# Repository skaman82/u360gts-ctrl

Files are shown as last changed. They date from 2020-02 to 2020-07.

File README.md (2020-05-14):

# u360gts-ctrl
u360gts Extension for the Mini-Case

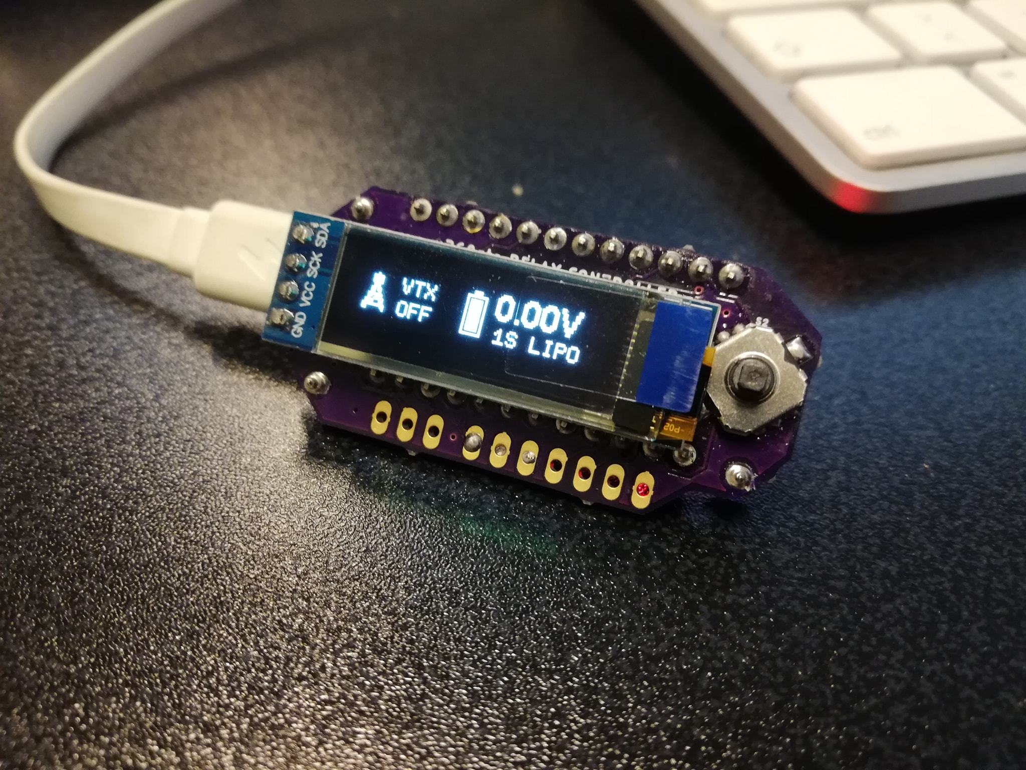
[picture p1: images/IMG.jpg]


This has the following functions:

• Turn ON/OFF the VTX</br>
• SmartAudio channel control (SA 2+ Version not supported, for unify nano you will need a 10k pull-down resistor on SA)</br>
• Battery monitoring</br>
• Controlls pan servo manually to allow to get to the screws of the case</br>
• Automatic parking mode to align the tracker again</br>

# PARTS
• Provided PCB

• Arduino Pro Micro (Leonardo) 3.3V
https://de.aliexpress.com/item/32992577032.html
If you have a 5V version, just replace the VREG on the board with this one: MIC5205-3.3YM5-TR

• 1206 4.7k resistor (R3)</br>
• 1206 27k resistor (R1)</br>
• 1206 100nf capacitor (C3)</br>
• 4x 0603 10k resistor (R2, R4, R5, R6)</br>
• 0603 1k resistor (R7)</br>
• IRLML6402 Mosfet (SOT23-3)</br>
• 2x BC848B Transistor (SOT23-3) (Q1, Q2)</br>

• 5-way tact switch
https://de.aliexpress.com/item/32860774374.html

• 128x32 I2C OLED Display
https://de.aliexpress.com/item/32965469301.html

• CD4066BM switch (SOP14 IC)
https://de.aliexpress.com/item/32461198916.html

• 3mm 940nm IR LEDs (receiver + transmitter) < 
receiver connects to GND and IR+ on the PCB; transmitter connects to 5v (through 100R resistor) and GND in the top box
https://de.aliexpress.com/item/32967272936.html

<strong>UPDATE 11. May 2020</strong><br>
Just spotted a bug on the PCB regarding the IR diode. I just corrected it in the new board file.
If you have the old version of the board, here is a workaround:<br><br>

• Remove R2 (don't throw it away)<br>
• bridge the two pads where R2 was sitting<br>
• solder the R2 to the outer side of the R6<br>
• connect 5V (BZ+) to the outer side of R2<br>
• Connect the IR LED (cathode on IR+, anode on IR-)<br>

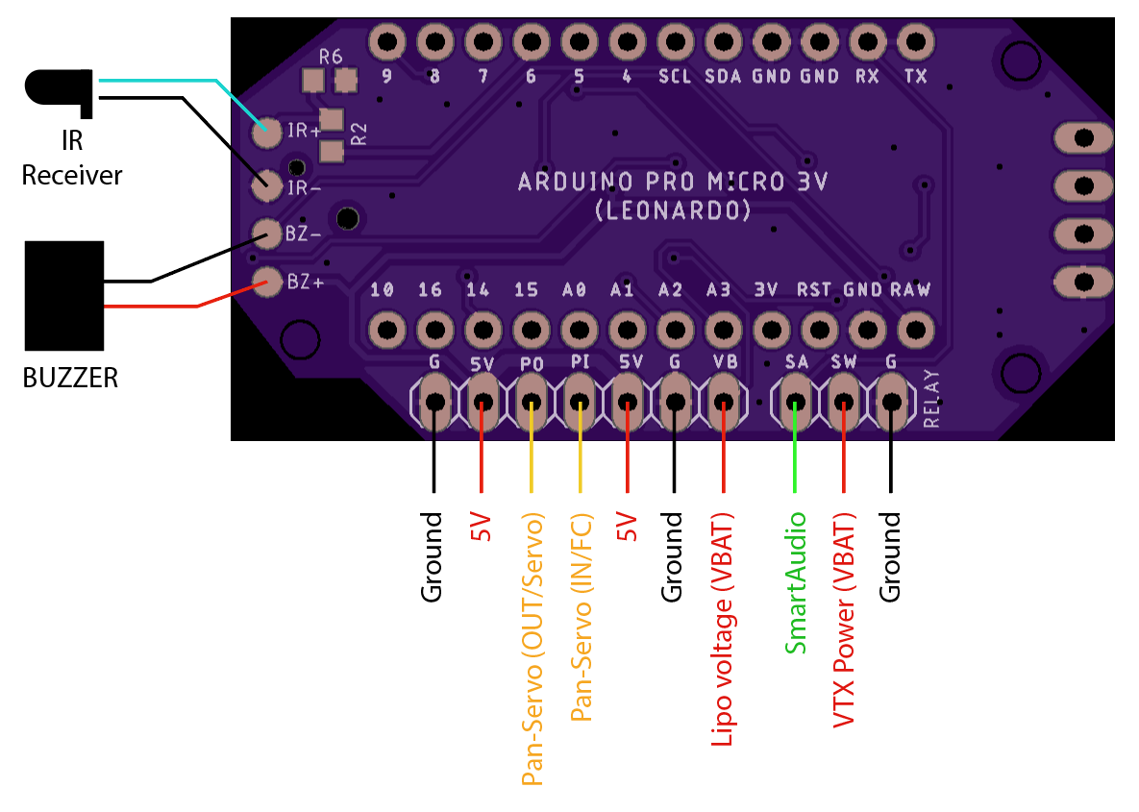
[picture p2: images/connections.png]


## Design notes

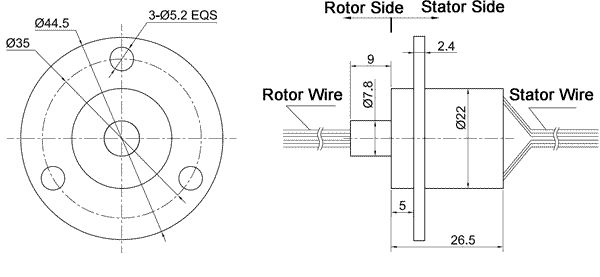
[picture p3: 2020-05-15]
images/slipring_sparkfun_senring.jpg

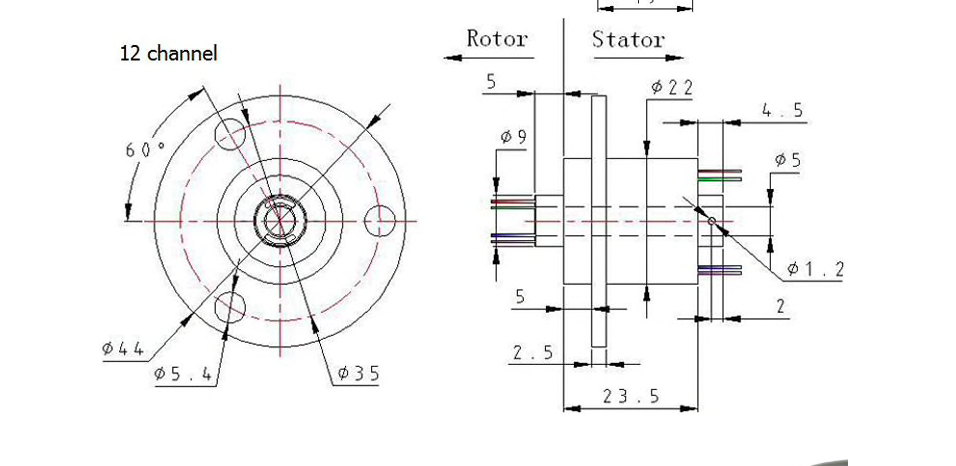
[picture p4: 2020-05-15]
images/slipring_ali.png

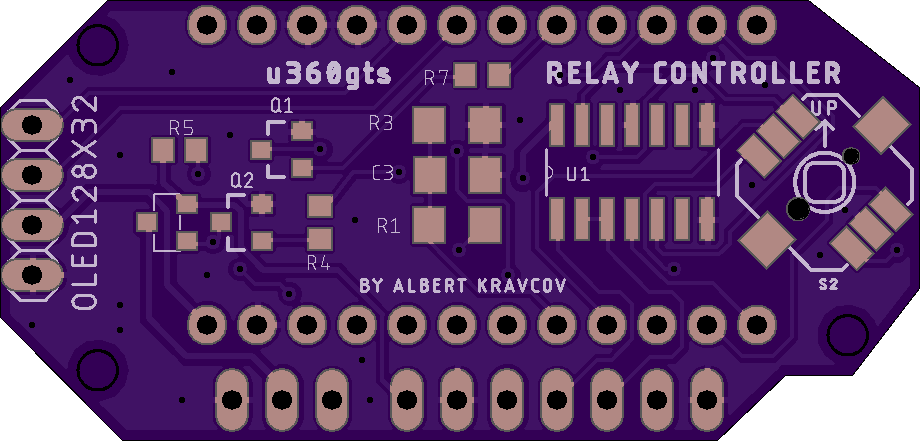
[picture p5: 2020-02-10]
images/Top.png

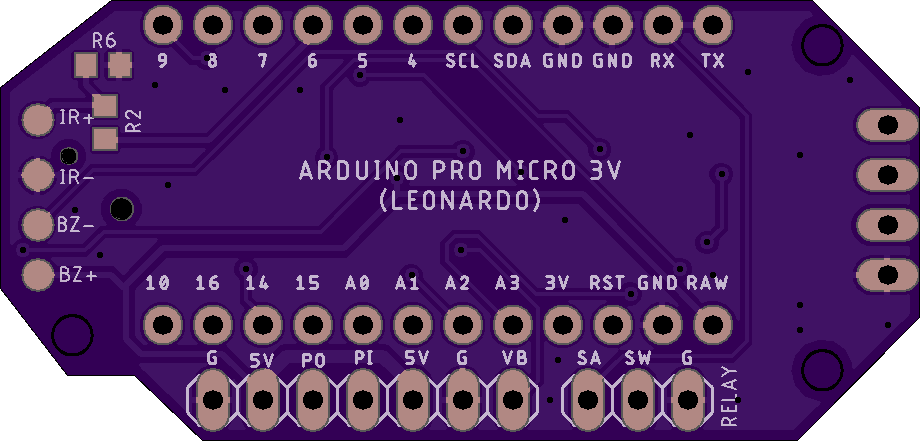
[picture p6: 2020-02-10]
images/Bottom.png

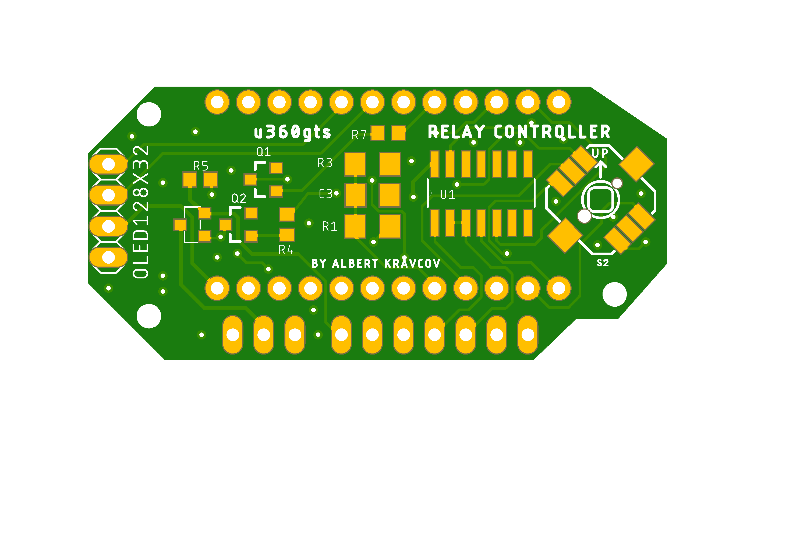
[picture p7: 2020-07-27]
PCB/RelayCTRL_t.png

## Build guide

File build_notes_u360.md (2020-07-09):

# u360gts *(mini build notes)*

### Features

- DIY antenna tracker based on u360gts by Raul Ortega  [https://github.com/raul-ortega/u360gts/](https://github.com/raul-ortega/u360gts/)
- compact design, only 75x75x100cm
- custom PCBs to simplify wiring
- modular tripod mounts
- supports 2-4S, XT60 connector
- 3.5mm analog Video-Out (Fatshark compatible)
- 6-Pin JST-SH breakout port (SW/RX/TX/5V/GND/VIDEO) to support:
  - telemetry relay to GS/tablet
  - connect external VTX
  - OpenLog via softserial
  - Bluetooth Module to configure u360gts
  - ...through 3 configurable pins(SW/RX/TX)
- 6-Pin JST-XH AV IO port (VIDEO/AUD_L/AUD_R/GND/VCC/GND) to connect an external RX-Module (i.e. FR632)
- intergrated Fatshark Module Bay on the head
- Telemetry input via Bluetooth or FSK-Modem, select via switch on head
- advanced controlling through u360gts-ctrl:
 - Turn ON/OFF the VTX
 - SmartAudio channel control
 - Battery monitoring
 - Manually control PAN (to access screws for example)
 - Infrared supported autonomous parking mode to align tracker
 - Bluetooth state-LED visible from outside

##### u360gts-ctrl

- manual PAN control via u360gts-ctl (to access the screws for example)
- Infrared supported Auto-Home position

## General build tips and notes

## u360gts Mini
#### Printing

Print files, PCBs and a complete bill of materials can be found here: https://www.thingiverse.com/thing:4108944

All parts are designed to be printed without supports (only supports touching build plate on some parts).

If your parts suffer from an elephant foot, decrease first layer flow, temperature, horizontal expansion and/or walls. Gear parts might not fit!

#### Assembly PCBs

UPDATE: Do NOT solder the buzzer to the PCB as as it can cause mag interference at this position. Place the buzzer somwhere at the bottom and wire it to the pads.

Isolate the back of the 128x64 display and remove the plastics on the pin headers for correct fit.

add a little button to the boot pins of the FC & thank me later
	
#### Assembly body

Prefit IR diode to the hole in the body-lid (used to reach home parking position) and if needed open hole with a drill. Same in the IR-LED in the bottom of the head.

Bottom left nut holder might needs a trim to ensure clearance to the 9pin header of the power PCB.

Place nuts early and fix with some glue.

The gears should not sit on each other and tilt the head to the side if correctly assembled.

#### Assembly head

Two versions of the slipring are currently supported. 23mm (AliExpress) and 26mm long (Sparkfun ROB-13065). Choose your "Bearing\_upper\_insert" STL accordingly.

Cut down the two little spars on the tilt servo so it seats flush on the wall

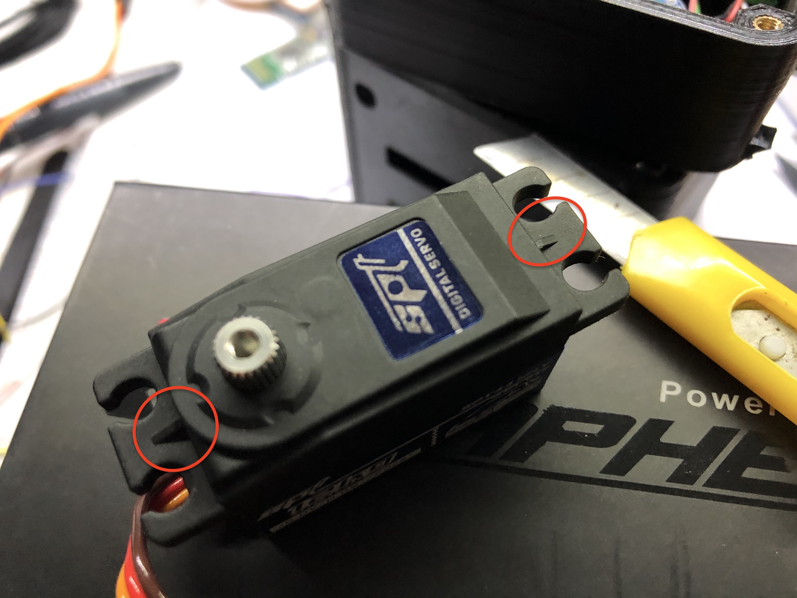
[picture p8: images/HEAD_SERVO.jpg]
Servo spars


Solder the IO board to the slipring from "behind" for easier cable routing

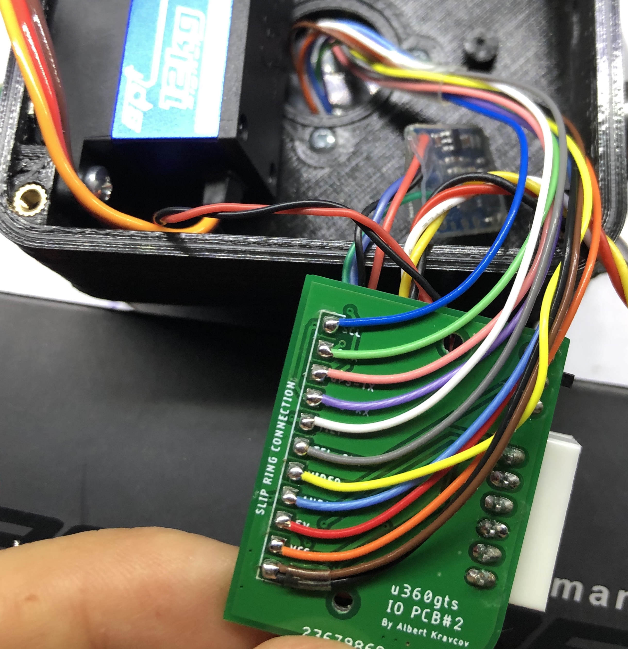
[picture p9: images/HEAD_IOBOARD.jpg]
IO board


Make sure all components (BT Module, RX Board etc.) are well isolated on the back to not create a short when closing the lid

Before mounting the servo-disc and the tracker arm, ensure the tilt servo is at 0° deg. If you dont own a servotester, connect to the GUI and move the servo using the slider. 

Once the arm is mounted, validate and adjust the tilt endpoints.

Note, the STATE Pin on the RX Board of the lid gets connected to the STATE Pin of your Bluetooth module and will switch on when connected.

#### Wiring

In general, try to route all cables below the FC when possible.

The Buzzer on the OLED board is connected to (+) through OLED-PCB and only needs GND to work. You can use BZ(+) to route 5V to the power PCB and then to power the CTRL board from the pads on top.

BZ(-) on the OLED board can be connected to the FC BZ(-) as well as the CTRL BZ(-) to run by both.

Only 11 pins between the body and the head are needed, use 2 cables for GND through the slipring

For PCBs prior 05/2020 you need to solder the diode in opposite direction (marking should be on the left).
	
Use a second 5V BEC for the PAN servo, as adviced in the partlist and wiring plan. 

RX/TX/SW on the Power PCB are currently not used. You can use those pads to route anything to the 6pin connector on the back (Relay VTX, openLog etc.)

Solder the wires of the OLED PCB to the slipring directing to the top of the PCB in a slight bow.

You can use some hot glue to fix the slipring wires to the pcb as the are fragile and they break easily at the solder joints 

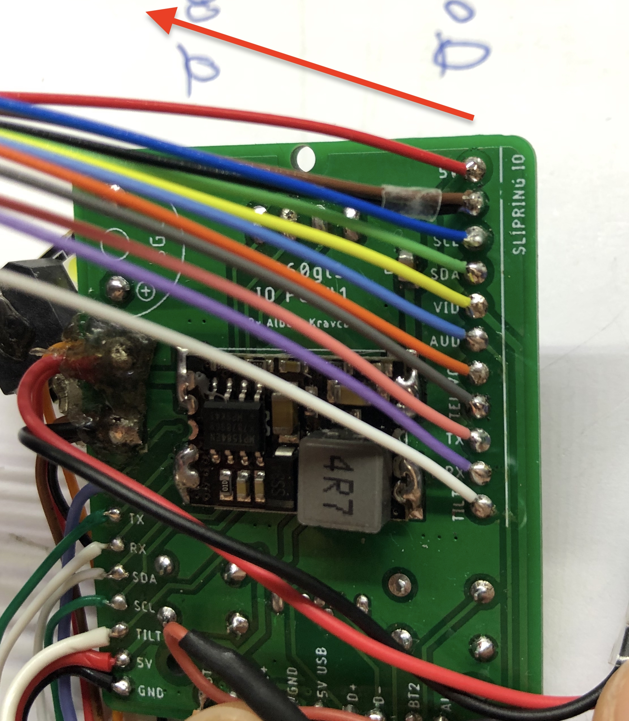
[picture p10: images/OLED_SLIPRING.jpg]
OLED to slipring

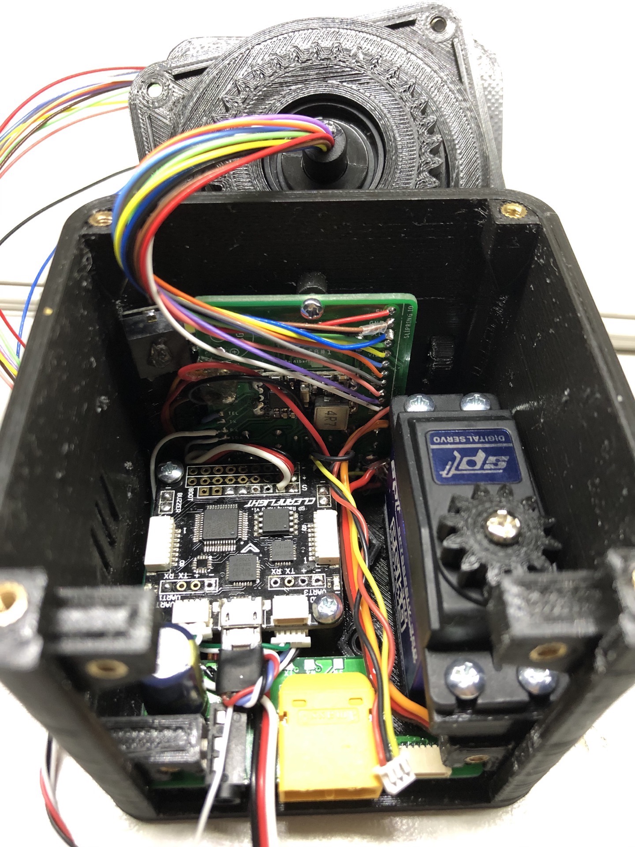
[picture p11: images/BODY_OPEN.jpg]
BODY


#### Wiring schema
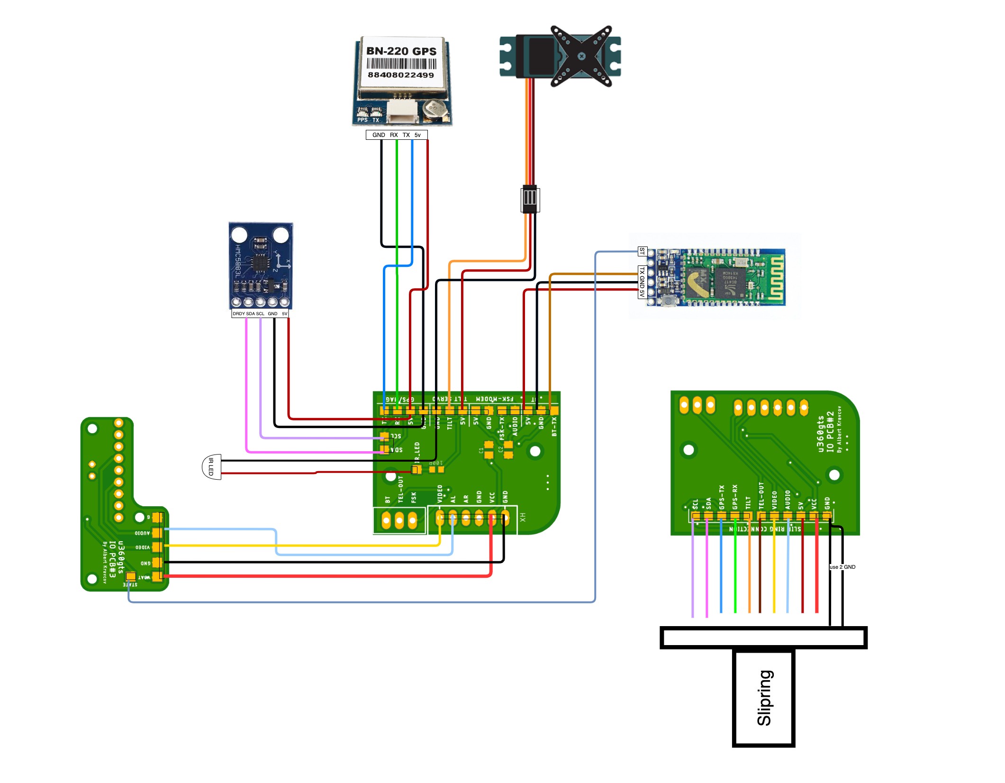
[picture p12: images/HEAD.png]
wiring head

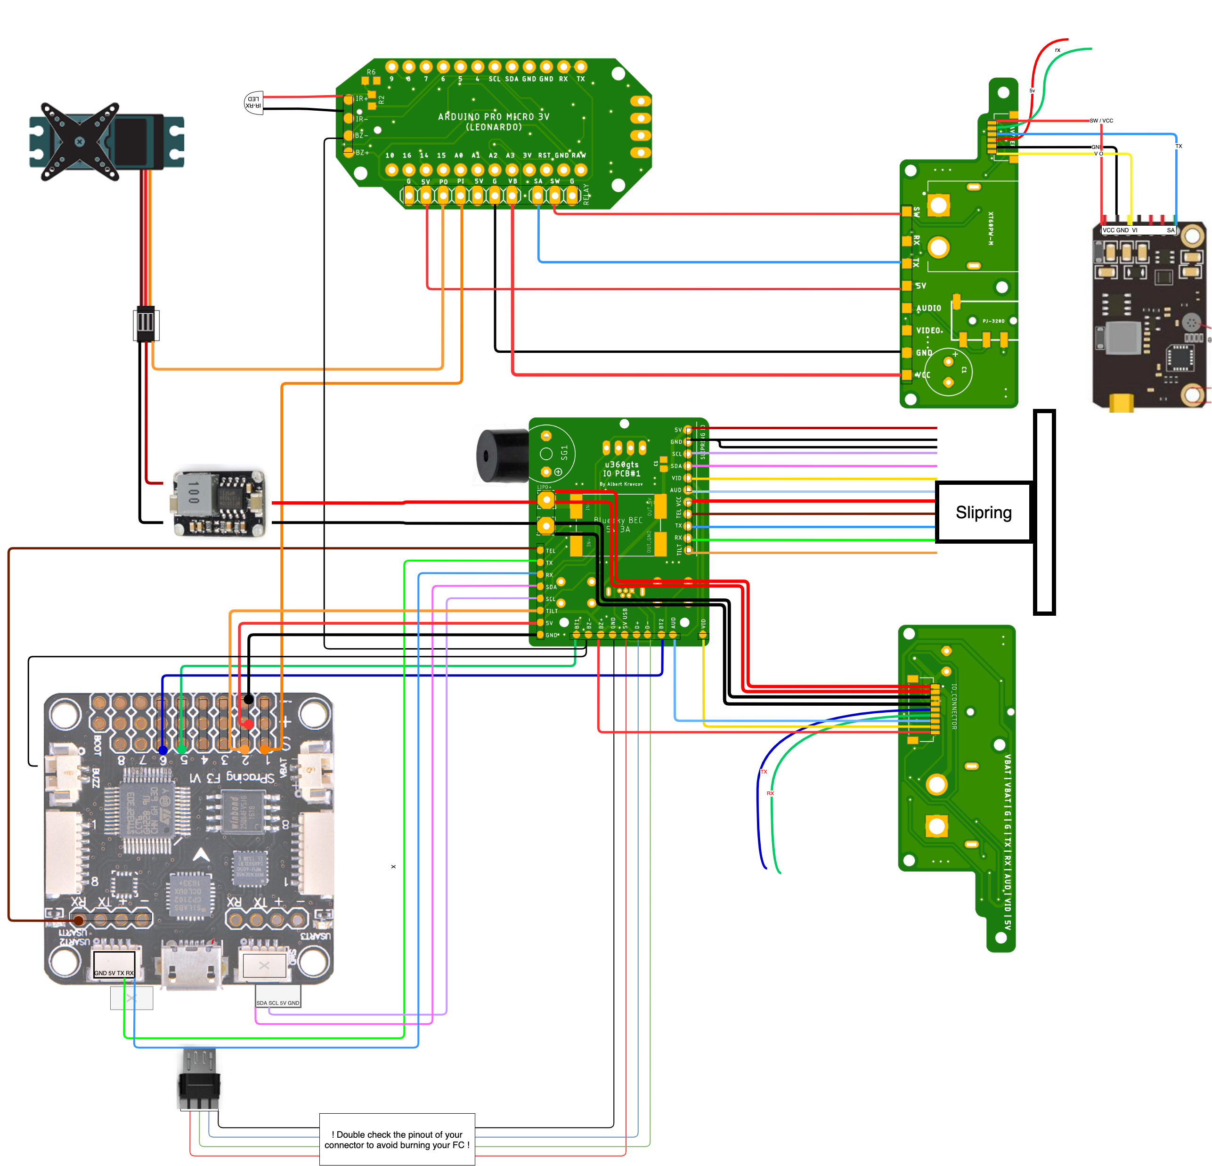
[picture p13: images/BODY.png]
wiring body


## u360gts Controller

#### Hardware

For PCBs prior 05/2020 you need to solder the IR emitter with reverse polarization. The boards also require a little hack to correct a routing mistake:<br>

• Remove R2 (don't throw it away)<br>
• bridge the two pads where R2 was sitting<br>
• solder the R2 to the outer side of the R6<br>
• connect 5V (BZ+) to the outer side of R2<br>
• Connect the IR LED (cathode on IR+, anode on IR-)<br>

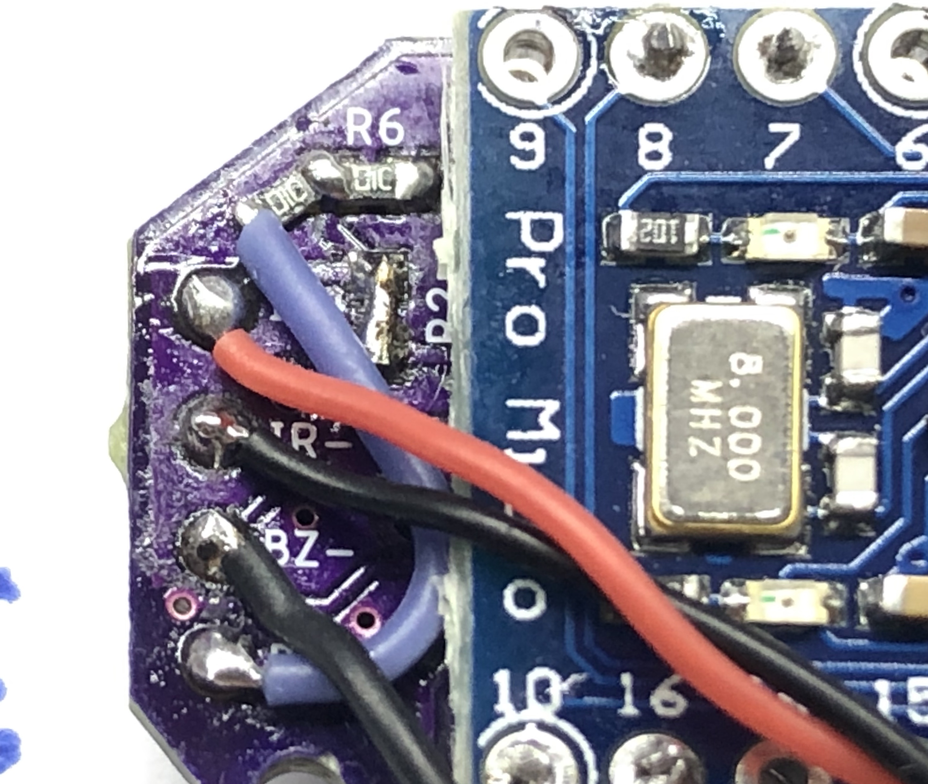
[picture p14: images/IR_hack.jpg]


Use two or three layer of electrical tape between Arduino Pro Micro and the PCB and remove the plastic spacers on the pin headers to ensure clearance to the gear section.

For TBS Unify Pro Nano, which uses SmartAudio Lite, connect a 10K resistor between SA and GND.

The 4066 switch on CTRL PCB with the edge DOWN, when the PCB shows upwards description.

**Important:** The CTRL will provide VCC to the VTX on the SW (switched) pad. Use a mini-BEC if a 5V VTX is planned (i.e. Pololu D24V3F)5 .

Handle the display with exta care. They seem to break easily. Maybe even get spares right away.

#### Software

If your PAN servo does move without command (in manual pan mode, or after the parking is completed), adjust **idle_servo** to match your servo-center-values.

Depending your choice of Arduino you might need to adjust the **voltage_scale**. If default _3.70_ does not match, try _5.56_

If home parking does not work, ensure IR diodes are working (see hardware section) and validate the IR reading in code. 

Enable the following lines in the Relay_CTRL.ino at line 1368-1269:

```
 //    Serial.println(ir_value); 
 //    delay(10); 
```

Then connect via the arduino IDE serial monitor should show the raw IR value like this during the parking process:

```
 522			<--- moving
 522			|
 521			|
 518			|
 452			<--- coming closer
 38				<--- reached ir_stop_value threshold, stops
```

#### Special Arduino Notes

on 3.3V/5V switchable Arduino Pro Micro (16Mhz resonator) use can use the Leonardo target.

on 3.3V fixed Arduinos (8Mhz resonator) follow this guide to enable the Sparkfun Pro Micro 3.3V/8Mhz target:
[https://learn.sparkfun.com/tutorials/pro-micro--fio-v3-hookup-guide/installing-mac--linux](https://github.com/raul-ortega/u360gts/blob/master/wiki/configuration-pan-servo.md)

In case you flashed with the wrong target, and your tty/cu/COM device disappeared, try to force to bootloader by shorting GND+RST twice. Your tty should appear for about 8 seconds to flash the correct hex.
This needs a good timing and might be tricky. 
You might want to extract the avrdude commands after settings the IDE to verbose, then pre-combile the sketch to .hex file and then write the .hex via avrdude manually.
This also works straight directly from Arduino IDE (klick upload, then short reset twice an the micro and it should find a com port and upload the code)

===

## GPS setup

#### Aircraft
Make sure your GPS Module has an update rate at least of 5 Hz

#### Tracker
Configure your Tracker GPS module as described here:
[https://github.com/raul-ortega/u360gts/blob/master/wiki/configuration-gps.md](https://github.com/raul-ortega/u360gts/blob/master/wiki/configuration-gps.md)

If you have a GPS installed and activated, you can set the "Minimun Number of Satellites" (8 is better) in the Configuratior for the home lock. The tracker will automatically determine home position after the set min sat count is reached. The "Continuous Home Update" setting is only usefull if you expecting to move the tracker mid flight.

===

## Telemetry setup

Remark: Telemetry input doesn't work with R9M ACCESS at this time. <br>
In this example I am using Crossfire. CRSF RX connected to an FC UART and serial RX is set to CRSF.
NOTE: CRSF telemetry is transfering a large amount of data. Because of that the BT link might be unstable. 

#### A simple telementy test (CROSSFIRE/X9D/WIRE)
Connect your radio the the flightcontroller via cable.

note: Serial Bridge via Cable through de-inverter ([https://oshpark.com/shared_projects/V3HPfIeN](https://oshpark.com/shared_projects/V3HPfIeN)) needs GND.

```
	Radio		 	 _______________		FC
	GND			|		| 	->	GND
	VCC	->		|  de-inverter	| 	->	n/a
	SIG			|_______________| 	->	RX on FC
```

Set the OpenTX Serial Port to "Telem Mirror" in the Hardware page of your radio settings. Choose CROSSFIRE protocol with baudrate 115200 on the u360gts.

**If "Telem Mirror" is not available, please upgrade your OpenTX later than 2.3x**

Connect a battery on your plane and wait until Sats are found. 

You should receive coordinates of the plane in the tracker now.

===

#### Bluetooth setup

Connect your BT module to an FTDI USB adapter.
Open Arduino serial terminal, make sure you baud 
rate matches the factory settings of the module.
Type AT and you should get an "OK" back if everything is working

The BT module might behave differently based on revision and firmware.

If you are using 2.4 videolink, bluetooth my interfere with your video signal - HC-12 may be a valid alterative as it is working on 433 MHz - it also has a better range (see below) 

##### How to bind a HC-05 FW 3.0 with a HC-05 FW 4.0

Both versions will blink every 2 second if AT mode is active

Get the configuration and address of both modules first.
colon (:) must be entered as comma (,)

###### Master (Radio) FW3.0
	- to enter AT mode no need to push the button, just connect EN and pull high from code
	- PIN needs to be "quoted"
	- request commands like AT+VERSION
	
	AT+VERSION
		3.0-20170601
	AT+NAME=X9D
	AT+UART=115200,0,0
	AT+ROLE=1
	AT+CMODE=1
	AT+PIN="1234"
	AT+ADDR=9999,88,F97D84
	AT+BIND=11,22,917BF

###### Slave (Tracker) FW4.0
	to enter AT mode I had to push the button when powering on
	no quotes around PIN
	request commands needed to end with ? like AT+VERSION?

	AT+VERSION?
		4.0-20190815
	AT+NAME=U360
	AT+UART=115200,0,0
	AT+ROLE=0
	AT+CMODE=0
	AT+PSWD=1234
	AT+ADDR=11,22,0917BF
	AT+BIND=9999,88,F97D84

###### validation commands:

	AT+VERSION?
	AT+NAME?
	AT+UART?
	AT+ROLE?
	AT+CMODE?
	AT+PSWD?
	AT+ADDR?
	AT+BIND?

=== 

##### How to bin a HM10 BLE Module connecting to Horus build-in BLE Module
(Version: HMSoft V533 or V610)<br>
You can check you version with AT+VERR? or AT+VERS?

Taranis side:
* Go to hardware menu and enable Bluetooth Telemetry
* Note the Local address of the BT module (from your radio screen)

HM10 Side:<br>
Connect your BT module to an FTDI USB adapter.
Open Arduino serial terminal, make sure you baud 
rate matches the factory settings of the module.
Type AT and you should get an "OK" back if everything is working

	* Make sure the password is 000000
	AT+PASS000000
	* Set the module to Central Role
	AT+ROLE1
	* Set the baud rate to 115200
	AT+BAUD4
	* Link the module to your radio by using the local address
	AT+CON4C249837C8F4 (replace numbers with your Mac address)

#### HC-12 (433MHz) Setup (HC-12_V2.3)

Connect your HC-12 module to an FTDI USB adapter (ground the SET pin).
Open Arduino serial terminal, make sure you baud 
rate matches the factory settings of the module.
Type AT and you should get an "OK" back if everything is working

	* change baudrate to 115200
	AT+B115200
	* Set the PowerMode FU3
	AT+FU3 
	* Change power level to +11dBm (25mw) - optional
	AT+P5
	* Change channel (always three numbers) - optional 
	AT+C001
	* Check your settings
	AT+RX

Remove ground from the SET pin. Configure the second module the same way.

## Software setup

1) connect via CLI and type "status", check for MAG="HMC5883"

```
System Uptime: 19 seconds, Voltage: 0 * 0.1V (3S battery - OK)
CPU Clock=72MHz, GYRO=MPU6050, ACC=MPU6050.n, MAG=HMC5883, GPS=2
Cycle Time: 1005, I2C Errors: 1, config size: 1928
```

2) calibrate PAN

   - see [https://github.com/raul-ortega/u360gts/blob/master/wiki/configuration-pan-servo.md](https://github.com/raul-ortega/u360gts/blob/master/wiki/configuration-pan-servo.md)
   - run the calibration in GUI
   - it should rotate counter-clock wise, stop, piep and then rotate clockwise
 
3) calibrate MAG 

  - see [https://github.com/raul-ortega/u360gts/blob/master/wiki/configuration-compass.md](https://github.com/raul-ortega/u360gts/blob/master/wiki/configuration-pan-servo.md)
  - set **offset** and **offset-trim** to 0 via CLI
  - fix your Mag PCB and dont touch/move it 
  - run the calibration in GUI
  - it should rotate at least 360 degrees here (lower starting calibration pulse if not)
    - depending on the result, set align_mag
    - save, reboot, re-calibrate
    - repeat until it directs North, OLED "H:" should be around 360/0
  - if your antenna does not point North now, adjust **offset** accordingly if the offset is less than 90 deg.
  - use align_mag CLI command if the tracker is not pointing north (following commands work: DEFAULT "CW0 CW90 CW180 CW270 CW0FLIP CW90FLIP CW180FLIP CW270FLIP"
  - it should try to point North if all works correctly now
  - fyi: offset-trim can be set while flying via the buttons when the aircraft is above min distance/altitude limits
 
4) run calibrate PAN again

  - [optionally] set the "startin Calibration Pulse" to 1100 to make it spin faster when calibrating in the field for example
  - re-run the calibration in GUI

5) setup telemetry
  - set your provider, i.e. iNav
  - choose your protocol (CROSSFIRE not available in GUI atm) and baudrate 115200

6) recommended features:

  - enable Tilt easing for soft start/stop
  - enable EPS to allow the tacker to *lead* the aircraft while moving (only usefull if telemetry update rate is very low)
  - decide how the tracke will get its home position: 
  You can set it manually with the push of the button when the aircraft has a GPS lock and is right in front of the tracker (default setting). The tracker will capture the position of the aircraft as its hime position. You can also let the tracker do this automatically if you select (Set Home: Auto, from telemetry) and set the "Minimum number of satellites" (8 is okay).

7) <strong>CRITICAL for operation:</strong> validate magnetometer/compass:

 - mount the tracker on a tripod, far away from everything that could cause magnetic interference and mout everything on it that will be mounted later while flying 
 - connect the tracker to the configurator
 - ensure the head is pointing north while connected to configurator
 - align the body of the tracker to the head
 - now enter 90/180/270 degree on the right side of the slider for PAN servo
 - validate if the outside walls align in each position
  - if they do: lucky man, you good to go
  - if they dont: calibrate mag, realign/improve mag position and/or add 10K pullup resistors between SDA and 5V, SCL and 5V, elevate the mag on a larger tower (three sizes on thingiverse) until the outside walls align at 0/90/180/270 deg.
  
## Operation when flying

- calibrate the Mag
- ensure video relay works
  - video from aircraft get received on tracker
  - video from tracker gets received on google
- wait for telemetry from aircraft and set HOME-POSITION when you got a 3D GPS fix (if not set to auto or it is done by the internal GPS)
- launch aircraft
- while in tracking mode you can use both buttons to correct the tracking by setting a negative or positive tracking offset.

## Troubleshooting

##### u360gts-configurator does not connect to tracker via USB #####

 - MSP baudrate is defined by the telemetry baudrate, choose 115200 via the buttons to match the COM/tty baudrate in the GUI
 - disconnect the BT module in the tracker when using USB if you have problems

##### Simulation mode not working #####

 - connect your tracker to power and USB to your computer
 - choose MAVLINK, bautrate 115200 in the u360
 - enable simulation mode, then connect to your tty/COM of the FC
 - choose MAVLINK in the UI, enter near by coordinates and some height
 - hit "start simulation"
    
##### Tracker "shakes" head / PAN moves when TILT moves #####

 - due to metall and other interference the mag might reports  ocillating data
 - try to relocate the mag-board to another location
 - replace metall with plastics where possible (screw inserts, screws, bearings) 
 - add 10K pullup resistors between SDA and 5V, SCL and 5V

### additional Resources:
 
  - [https://github.com/raul-ortega/u360gts/blob/master/wiki/configuration-quick-start-guide.md](https://github.com/raul-ortega/u360gts/blob/master/wiki/configuration-quick-start-guide.md)
  - [PCB to de-invert Taranis Telemetry for Bluetooth](https://oshpark.com/shared_projects/V3HPfIeN)

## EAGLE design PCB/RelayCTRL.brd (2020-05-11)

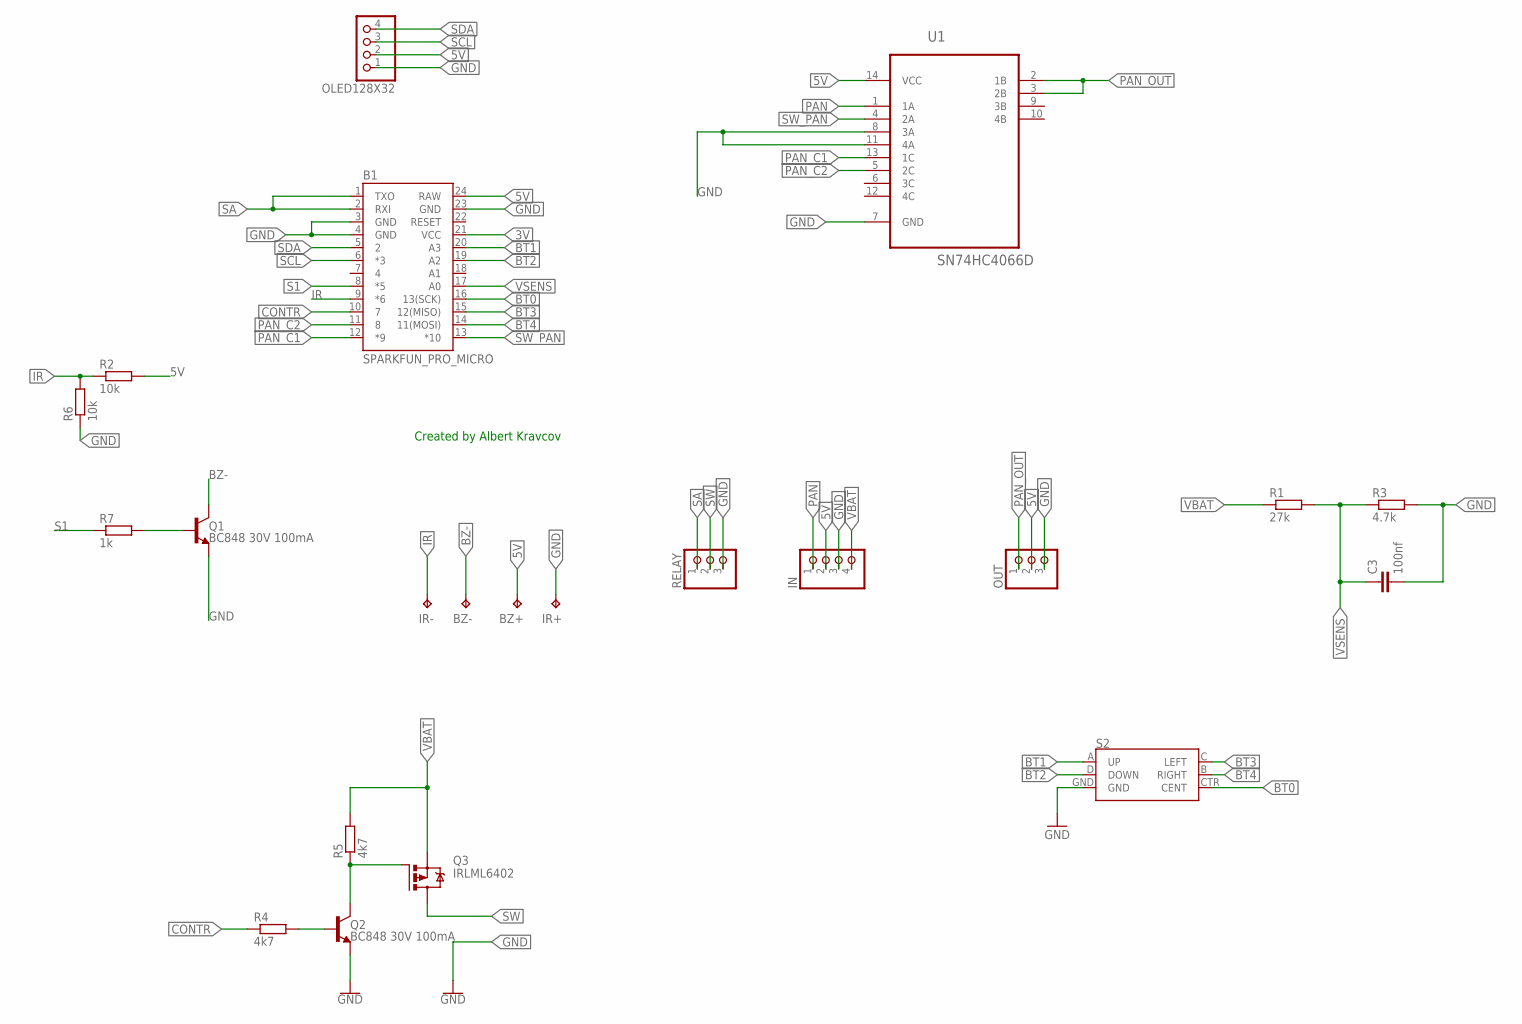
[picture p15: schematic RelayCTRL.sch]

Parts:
B1: SPARKFUN_PRO_MICRO
BZ+: TPTP15R; TP15R
BZ-: TPTP15R; TP15R
C3: 100nf; C1206
IN: PINHD-1X4; 1X04
IR+: TPTP15R; TP15R
IR-: TPTP15R; TP15R
OLED128X32: PINHD-1X4; 1X04
OUT: PINHD-1X3; 1X03
Q1, Q2: BC848 30V 100mA; SOT23-3
Q3: IRLML6402; MICRO3
R1: 27k; R1206
R2, R6: 10k; R0603
R3: 4.7k; R1206
R4, R5: 4k7; R0603
R7: 1k; R0603
RELAY: PINHD-1X3; 1X03
S2: JOYSTICK_MINI
U1: SN74HC4066D; SOIC127P600X175-14N

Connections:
3V: B1.21 (VCC)
5V: B1.24 (RAW), BZ+.TP, IN.2, OLED128X32.2, OUT.2, R2.2, U1.14 (VCC)
BT0: B1.16 (13(SCK)), S2.CTR (CENT)
BT1: B1.20 (A3), S2.A (UP)
BT2: B1.19 (A2), S2.D (DOWN)
BT3: B1.15 (12(MISO)), S2.C (LEFT)
BT4: B1.14 (11(MOSI)), S2.B (RIGHT)
BZ-: BZ-.TP, Q1.3 (C)
CONTR: B1.10 (7), R4.1
GND: B1.3 (GND), B1.4 (GND), B1.23 (GND), C3.2, IN.3, IR+.TP, OLED128X32.1, OUT.3, Q1.2 (E), Q2.2 (E), R3.2, R6.1, RELAY.3, S2.GND, U1.7 (GND), U1.8 (3A), U1.11 (4A)
IR: B1.9 (*6), IR-.TP, R2.1, R6.2
unnamed: Q2.1 (B), R4.2
unnamed: Q2.3 (C), Q3.1 (G), R5.1
unnamed: Q1.1 (B), R7.2
PAN: IN.1, U1.1 (1A)
PAN_C1: B1.12 (*9), U1.13 (1C)
PAN_C2: B1.11 (8), U1.5 (2C)
PAN_OUT: OUT.1, U1.2 (1B), U1.3 (2B)
S1: B1.8 (*5), R7.1
SA: B1.1 (TXO), B1.2 (RXI), RELAY.1
SCL: B1.6 (*3), OLED128X32.3
SDA: B1.5 (2), OLED128X32.4
SW: Q3.3 (D), RELAY.2
SW_PAN: B1.13 (*10), U1.4 (2A)
VBAT: IN.4, Q3.2 (S), R1.1, R5.2
VSENS: B1.17 (A0), C3.1, R1.2, R3.1

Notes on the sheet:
Created by Albert Kravcov

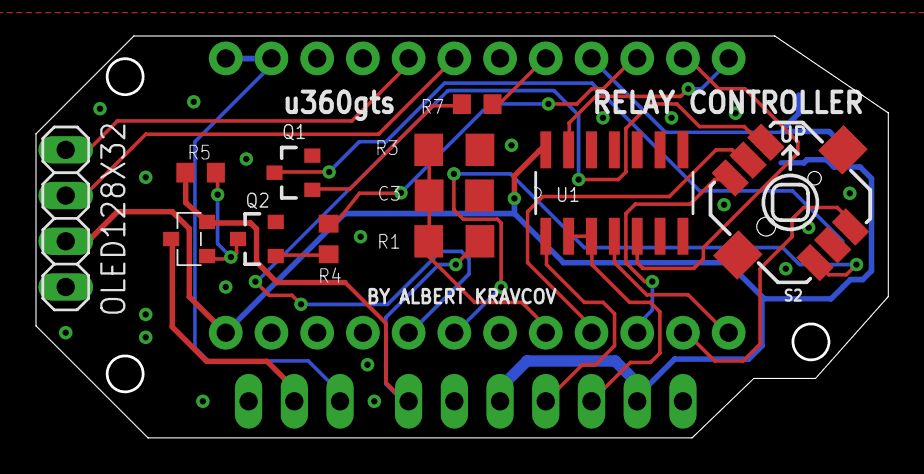
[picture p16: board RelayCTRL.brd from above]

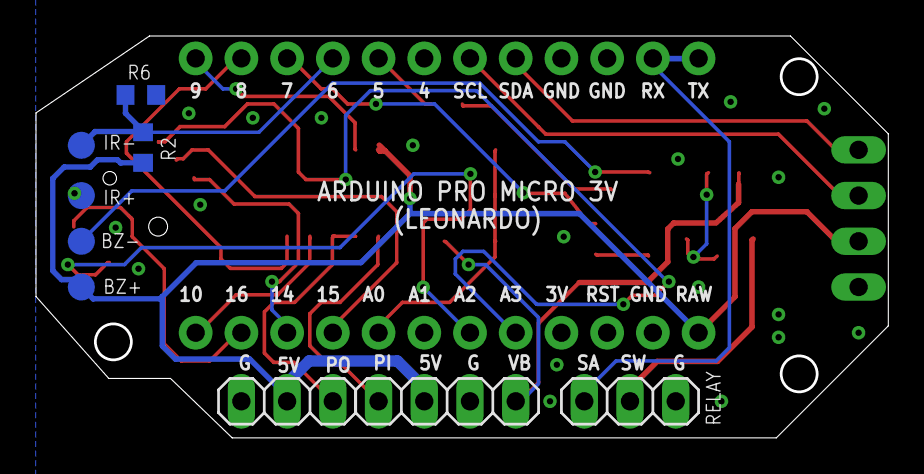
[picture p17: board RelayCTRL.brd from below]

Board: 2 copper layers, 47.4 x 22.3 mm, 22 parts (10 on the bottom side), 25 nets.

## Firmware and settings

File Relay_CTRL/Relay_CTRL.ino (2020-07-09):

// Created by Albert Kravcov
// SmartAudio code is adapted from Lukas Blocher https://github.com/NightHawk32/SmartAudio-testing
// Target: Sparkfun Pro Micro, 3.3V, 8MHz (if you have the switchable version then select 5V, 16MHz even if it is set to 3V!)
//https://raw.githubusercontent.com/sparkfun/Arduino_Boards/master/IDE_Board_Manager/package_sparkfun_index.json

#include <HardwareSerial.h>
#include <EEPROM.h>
#include <Servo.h>
#include "U8glib.h" //Install U8glib Library to be able to compile
#include "bitmaps.h"

Servo myservo;  // create servo object to control a servo D9

U8GLIB_SSD1306_128X32 u8g(U8G_I2C_OPT_NONE);  // I2C / TWI


// USER SETTINGS START >>

#define voltage_scale   3.70  //play with this number to adjust voltage scale
#define idle_servo      1500  //center value for the pan servo in us
#define ir_stop_value   41    //value limit of the IR sensor for parking
#define SERVO_MG995           //select servo type accoringly: SERVO_SPT or SERVO_MG995 

// >> USER SETTINGS END 


#define peraypwrADDR    1       // EEPROM Adress
#define R1              27000   // Resistor1 27k
#define R2              4700    // Resistor2 4.7k
#define bt_ct           15      //Center Button
#define bt_le           14      //Left Button
#define bt_ri           16      //Right Button
#define bt_up           21      //Up Button
#define bt_down         20      //Down Button
#define vbat_pin        A0      //vsens pin
#define ir_pin          A7      //IR receiver pin
#define pwm_contr1      8       //4066 c1 
#define pwm_contr2      9       //4066 c2
#define pwm_pin         10      //Servo signal pin
#define ctrl_pin        7       //Mosfet controll - VTX power control
#define BZ_pin          5       //Optional Buzzer
#define RXLED           17      // The RX LED has a defined Arduino pin
#define TXLED           30      // The TX LED has a defined Arduino pin

int act_freq;
byte act_band = 0;
byte act_ch = 1;
byte cur_pos = 0;
byte vsens_value = 15;
byte SA_available = 0;
byte sa_update = 0;
byte parking_step = 0;
int ir_value;
byte pressedbut = 0;
byte i_butt = 0;
int vsens;
float voltage;
float cellvoltage;
byte celldetect = 0;
byte menuactive = 0;
long previousMillis = 0;
long buzzermillis = 0;
byte relaypower = 0;
byte alarmstate;


//SA SETUP -------------------------------------------
uint8_t buff[25];
uint8_t rx_len = 0;
uint8_t zeroes = 0;
int incomingByte = 0;

#define SA_GET_SETTINGS 0x01
#define SA_GET_SETTINGS_V2 0x09
#define SA_SET_POWER 0x02
#define SA_SET_CHANNEL 0x03
#define SA_SET_FREQUENCY 0x04
#define SA_SET_MODE 0x05

#define SA_POWER_25MW 0
#define SA_POWER_50MW 1
#define SA_POWER_200MW 2
#define SA_POWER_800MW 3

enum SMARTAUDIO_VERSION {
  NONE,
  SA_V1,
  SA_V2
};

static const uint8_t V1_power_lookup[] = {
  7,
  16,
  25,
  40
};

typedef struct {
  SMARTAUDIO_VERSION vtx_version;
  uint8_t channel;
  uint8_t powerLevel;
  uint8_t mode;
  uint16_t frequency;

} UNIFY;

static UNIFY unify;

uint8_t crc8(const uint8_t *data, uint8_t len)
{
#define POLYGEN 0xd5
  uint8_t crc = 0;
  uint8_t currByte;

  for (int i = 0 ; i < len ; i++) {
    currByte = data[i];
    crc ^= currByte;
    for (int i = 0; i < 8; i++) {
      if ((crc & 0x80) != 0) {
        crc = (byte)((crc << 1) ^ POLYGEN);
      } else {
        crc <<= 1;
      }
    }
  }
  return crc;
}

static void sa_tx_packet(uint8_t cmd, uint32_t value) {
  //here: length --> only payload, without CRC
  //here: CRC --> calculated for complete packet 0xAA ... payload
  uint8_t buff[10];
  uint8_t packetLength = 0;
  buff[0] = 0x00;
  buff[1] = 0xAA; //sync
  buff[2] = 0x55; //sync
  buff[3] = (cmd << 1) | 0x01; //cmd

  switch (cmd) {
    case SA_GET_SETTINGS:
      buff[4] = 0x00; //length
      buff[5] = crc8(&buff[1], 4);
      buff[6] = 0x00;
      packetLength = 7;
      break;
    case SA_SET_POWER:
      buff[4] = 0x01; //length
      buff[5] = (unify.vtx_version == SA_V1) ? V1_power_lookup[value] : value;
      buff[6] = crc8(&buff[1], 5);
      buff[7] = 0x00;
      packetLength = 8;
      break;
    case SA_SET_CHANNEL:
      buff[4] = 0x01; //length
      buff[5] = value;
      buff[6] = crc8(&buff[1], 5);
      buff[7] = 0x00;
      packetLength = 8;
      break;
    case SA_SET_FREQUENCY:
      buff[4] = 0x02;
      buff[5] = (value >> 8); //high byte first
      buff[6] = value;
      buff[7] = crc8(&buff[1], 6);
      buff[8] = 0x00;
      packetLength = 9;
      break;
    case SA_SET_MODE: //supported for V2 only: UNIFY HV and newer
      if (unify.vtx_version == SA_V2) {
        //TBD --> Pit mode
        /*
          buffer[4] = 0x01; //length
          buffer[5] = value;
          buffer[6] = crc8(&buffer[1], 5);
          buffer[7] = 0x00;
          packetLength = 8;s
        */
      }
      break;
  }
  for (int i = 0; i < packetLength; i++) {
    Serial1.write(buff[i]);
  }
}

static void sa_rx_packet(uint8_t *buff, uint8_t len) {
  //verify packet
  uint8_t packetStart = 0;
  for (int i = 0; i < len - 3; i++) {
    if (buff[i] == 0xAA && buff[i + 1] == 0x55 && buff[i + 3] < len) {
      packetStart = i + 2;
      uint8_t len = buff[i + 3];
      uint8_t crcCalc = crc8(&buff[i + 2], len + 1);
      uint8_t crc = buff[i + 3 + len];

      if (crcCalc == crc) {
        //Serial.println("CRC match");
        switch (buff[packetStart]) {
          case SA_GET_SETTINGS: //fall-through
          case SA_GET_SETTINGS_V2:
            //Serial.println("SA_GET_SETTINGS");
            unify.vtx_version = (buff[packetStart] == SA_GET_SETTINGS) ? SA_V1 : SA_V2;
            packetStart += 2; //skip cmd and length
            unify.channel = buff[packetStart++];
            unify.powerLevel = buff[packetStart++];
            unify.mode = buff[packetStart++];
            unify.frequency = ((uint16_t)buff[packetStart++] << 8) | buff[packetStart++];
            break;
          case SA_SET_POWER:
            //Serial.println("SA_SET_POWER");
            packetStart += 2;
            unify.powerLevel = buff[packetStart++];
            break;
          case SA_SET_CHANNEL:
            //Serial.println("SA_SET_CHANNEL");
            packetStart += 2;
            unify.channel = buff[packetStart++];
            break;
          case SA_SET_FREQUENCY:
            //Serial.println("SA_SET_FREQUENCY");
            //TBD: Pit mode Freq
            packetStart += 2;
            unify.frequency = ((uint16_t)buff[packetStart++] << 8) | buff[packetStart++];
            break;
          case SA_SET_MODE:
            //SA V2 only!
            break;
        }
        return;

      } else {
        //Serial.println("CRC mismatch");
        return;
      }
    }
  }

}

//SA SETUP END -------------------------------------------




void setup(void) {
  if ( u8g.getMode() == U8G_MODE_R3G3B2 ) {
    u8g.setColorIndex(255);     // white
  }
  else if ( u8g.getMode() == U8G_MODE_GRAY2BIT ) {
    u8g.setColorIndex(3);         // max intensity
  }
  else if ( u8g.getMode() == U8G_MODE_BW ) {
    u8g.setColorIndex(1);         // pixel on
  }
  else if ( u8g.getMode() == U8G_MODE_HICOLOR ) {
    u8g.setHiColorByRGB(255, 255, 255);
  }

  analogReference(DEFAULT); //INTERNAL 2.56 or DEFAULT 3.3

  Serial.begin(9600);
  //while (!Serial);  // Leonardo: wait for serial monitor
  //Serial.println("SerialReady");

  Serial1.begin(4900, SERIAL_8N2);
  UCSR1B &= ~(1 << TXEN1);

  pinMode(bt_ri, INPUT_PULLUP); //BT right
  pinMode(bt_ct, INPUT_PULLUP); //BT center
  pinMode(bt_le, INPUT_PULLUP); //BT left
  pinMode(bt_up, INPUT_PULLUP); //BT up
  pinMode(bt_down, INPUT_PULLUP); //BT down
  pinMode(ctrl_pin, OUTPUT); //VTX SW
  pinMode(vbat_pin, INPUT); //VSENS A0
  pinMode(ir_pin, INPUT); //IR INPUT (D6/A7)
  pinMode(pwm_contr1, OUTPUT); //CONTROL A 4066
  pinMode(pwm_contr2, OUTPUT); //CONTROL B 4066
  pinMode(BZ_pin, OUTPUT); //BZ- PAD

  //pinMode(RXLED, OUTPUT); 
  //pinMode(TXLED, OUTPUT); 

  myservo.attach(pwm_pin); //SW SERVO OUTPUT

  relaypower = EEPROM.read(peraypwrADDR);

  if (relaypower > 1)
  {
    relaypower = 1;
  }

  clearOLED();
}



byte buttoncheck()
{
  int i_butt = 0;
  byte buttonz = 0;
  if (digitalRead(bt_ri) != 1) {
    while (digitalRead(bt_ri) != 1)
    {
      delay(2);
      i_butt++;
    }
    buttonz = 1; //Right pressed
  }

  else if (digitalRead(bt_ct) != 1) {
    while (digitalRead(bt_ct) != 1) {
      delay(2);
      i_butt++;
    }
    buttonz = 2; //Center pressed
  }
  else if (digitalRead(bt_le) != 1) {
    while (digitalRead(bt_le) != 1) {
      delay(2);
      i_butt++;
    }
    buttonz = 3; //Left pressed
  }
  else if (digitalRead(bt_up) != 1) {
    while (digitalRead(bt_up) != 1) {
      delay(2);
      i_butt++;
    }
    buttonz = 4; //Up pressed
  }
  else if (digitalRead(bt_down) != 1) {
    while (digitalRead(bt_down) != 1) {
      delay(2);
      i_butt++;
    }
    buttonz = 5; //Down pressed
  }  
  pressedbut = buttonz;
  return buttonz;
}



void clearOLED()
{
  u8g.firstPage();
  do
  {
  }
  while ( u8g.nextPage() );
}





//MAIN LOOP

void loop(void) {
  u8g.firstPage();
  do {

    buttoncheck();
    SAcontrol();
    ReadVoltage();
    relay_ctrl();
    parking_ctrl();

    u8g.setFont(u8g_font_helvB12r);

    if (celldetect == 0) {
      u8g.setPrintPos(65, 16);
      u8g.setFont(u8g_font_6x10r);
      u8g.print("READING");
      u8g.setPrintPos(65, 27);
      u8g.print("VOLTAGE");
    }

    else {
      u8g.setPrintPos(73, 17);
      u8g.print(voltage);
      u8g.print("V");

      u8g.setPrintPos(75, 28);
      u8g.setFont(u8g_font_6x10r);
      u8g.print(celldetect);
      u8g.print("S LIPO");

      u8g.drawFrame (58, 8, 10, 19);
      u8g.drawBox (61, 6, 4, 2);

      if (cellvoltage >= 3.97) {
        u8g.drawBox (60, 10, 6, 3);
        u8g.drawBox (60, 14, 6, 3);
        u8g.drawBox (60, 18, 6, 3);
        u8g.drawBox (60, 22, 6, 3);
      }
      else if ((cellvoltage < 3.97) && (cellvoltage >= 3.75)) {
        u8g.drawBox (60, 14, 6, 3);
        u8g.drawBox (60, 18, 6, 3);
        u8g.drawBox (60, 22, 6, 3);
      }
      else if ((cellvoltage < 3.75) && (cellvoltage >= 3.52)) {
        u8g.drawBox (60, 18, 6, 3);
        u8g.drawBox (60, 22, 6, 3);
      }
      else if ((cellvoltage < 3.52) && (cellvoltage >= 3.33)) {
        u8g.drawBox (60, 22, 6, 3);
      }
      else if (cellvoltage < 3.33) {

        unsigned long buzzertime = millis();
        if (buzzertime - buzzermillis > 1000) { // one second loop
          buzzermillis = buzzertime;
          if (alarmstate == 0) {
            alarmstate = 1;
            tone(BZ_pin, 200, 200); //beep for 200ms
          }
          else {
            alarmstate = 0;
            noTone(BZ_pin); //no beep

          }
        }
      }


      //ALARM INDICATOR FUNCTION

      if (alarmstate == 0) {
        //digitalWrite(TXLED, HIGH);
      }
      else if (alarmstate == 1) {
        //digitalWrite(TXLED, LOW);
        u8g.drawBox (60, 10, 6, 15);
      }


    }

    if (relaypower == 1) {

      u8g.drawBitmapP(3, 0, 3, 30, bitmap_relayON);

      if (SA_available == 0) {
        u8g.setPrintPos(28, 15);
        u8g.setFont(u8g_font_6x10r);
        u8g.print("NO");
        u8g.setPrintPos(28, 26);
        u8g.print("SA");
      }
      else {

        u8g.setPrintPos(26, 17);
        u8g.setFont(u8g_font_helvB12r);
        if (act_band == 0) {
          u8g.print("A");
        }
        else if (act_band == 1) {
          u8g.print("B");
        }
        else if (act_band == 2) {
          u8g.print("E");
        }
        else if (act_band == 3) {
          u8g.print("F");
        }
        else if (act_band == 4) {
          u8g.print("R");
        }

        u8g.setPrintPos(39, 17);
        u8g.print(act_ch);
        u8g.setPrintPos(26, 28);
        u8g.setFont(u8g_font_6x10r);
        u8g.print(act_freq);
      }
    }

    else {
      u8g.drawBitmapP(3, 2, 3, 30, bitmap_relayOFF);
      u8g.setPrintPos(25, 15);
      u8g.setFont(u8g_font_6x10r);
      u8g.print("VTX");
      u8g.setPrintPos(25, 26);
      u8g.print("OFF");
    }

    if (pressedbut == 2) {
      menu();
    }


  } while ( u8g.nextPage() );
}

//LOOP END




void menu() {
  menuactive = 1;
  byte exit = 0;
  clearOLED();
  SAcontrol();

  while (exit == 0) {

    u8g.firstPage();
    do {
      buttoncheck();

      if (menuactive == 1) {
        u8g.setFont(u8g_font_6x10r);
        u8g.setPrintPos(10, 19);
        u8g.print("AV-RELAY POWER >");

        if (pressedbut == 1) {
          menuactive = 2;
        }
        if (pressedbut == 2) {
          pwr_screen();
        }
        if (pressedbut == 3) {
          menuactive = 4;
        }
      }


      else if (menuactive == 2) {
        u8g.setFont(u8g_font_6x10r);
        u8g.setPrintPos(10, 19);
        u8g.print("AV-RELAY CHANNEL >");

        if (pressedbut == 1) {
          menuactive = 3;
        }
        if (pressedbut == 3) {
          menuactive = 1;
        }
        if (pressedbut == 2) {
          vtx_screen();
        }
      }


      else if (menuactive == 3) {
        u8g.setFont(u8g_font_6x10);
        u8g.setPrintPos(10, 19);
        u8g.print("TRACKER PARKING >");

        if (pressedbut == 1) {
          menuactive = 4;
        }
        if (pressedbut == 3) {
          menuactive = 2;
        }
        if (pressedbut == 2) {
          parking_screen();
        }
      }


      else if (menuactive == 4) {
        u8g.setFont(u8g_font_6x10);
        u8g.setPrintPos(10, 19);
        u8g.print("MANUAL PAN >");

        if (pressedbut == 1) {
          menuactive = 5;
        }
        if (pressedbut == 3) {
          menuactive = 3;
        }
        if (pressedbut == 2) {
          menuactive = 0;
          manctrl_screen();

        }
      }

      else if (menuactive == 5) {
        u8g.setFont(u8g_font_6x10);
        u8g.setPrintPos(10, 19);
        u8g.print("EXIT");

        if (pressedbut == 1) {
          menuactive = 1;
        }
        if (pressedbut == 3) {
          menuactive = 4;
        }
        if (pressedbut == 2) {
          return;
        }
      }

      if (menuactive == 0) {
        return;
      }


    } while ( u8g.nextPage() );


  }
}


void pwr_screen(void) {
  byte exit = 0;
  menuactive = 0;
  cur_pos = 0;
  clearOLED();

  while (exit == 0) {

    u8g.firstPage();
    do {

      buttoncheck();
      relay_ctrl();

      u8g.setPrintPos(8, 20);
      u8g.setFont(u8g_font_helvB12r);

      if (relaypower == 1) {

        u8g.print("VTX ON");
      }
      else {
        u8g.print("VTX OFF");
      }

      if (cur_pos == 0) {
        u8g.setFont(u8g_font_6x10);
        u8g.drawFrame (88, 6, 33, 19);
        u8g.setPrintPos(93, 19);
        u8g.print("EXIT");
        u8g.drawBox (8, 24, 70, 2);
      }


      else if (cur_pos == 1) {
        u8g.setFont(u8g_font_6x10);
        u8g.drawBox (88, 6, 33, 19);
        u8g.setColorIndex(0);
        u8g.setPrintPos(93, 19);
        u8g.print("EXIT");
        u8g.setColorIndex(1);
      }

      if (pressedbut == 1) {
        if (cur_pos < 1 ) {
          cur_pos = cur_pos + 1;
        }
        else {
          cur_pos = 0;
        }
      }

      if (pressedbut == 3) {
        if (cur_pos > 0 ) {
          cur_pos = cur_pos - 1;
        }
        else {
          cur_pos = 1;
        }
      }

      if (pressedbut == 2) {
        if (cur_pos == 1) {
          sa_update = 0;
          EEPROM.write(peraypwrADDR, relaypower);
          return;

        }
        else if (cur_pos == 0) {
          if (relaypower == 1) {
            relaypower = 0;
          }
          else {
            relaypower = 1;
          }
        }
      }


    } while ( u8g.nextPage() );

  }
}



void parking_screen(void) {
  byte exit = 0;
  menuactive = 0;
  cur_pos = 0;
  clearOLED();
  parking_step = 0;

  while (exit == 0) {
    u8g.firstPage();
    do {

      buttoncheck();
      parking_ctrl();


      if (parking_step == 0) {
        u8g.setPrintPos(5, 13);
        u8g.print("START");
        u8g.setPrintPos(5, 24);
        u8g.print("PARKING?");


        if (cur_pos == 0) {
          u8g.drawBox (63, 6, 25, 19);
          u8g.setColorIndex(0);
          u8g.setPrintPos(70, 19);
          u8g.print("NO");
          u8g.setColorIndex(1);
          u8g.setFont(u8g_font_6x10);
          u8g.drawFrame (88, 6, 33, 19);
          u8g.setPrintPos(96, 19);
          u8g.print("YES");

          if (pressedbut == 2) {
            return;
          }
        }


        else if (cur_pos == 1) {
          u8g.drawFrame (63, 6, 25, 19);
          u8g.setPrintPos(70, 19);
          u8g.print("NO");
          u8g.setFont(u8g_font_6x10);
          u8g.drawBox (88, 6, 33, 19);
          u8g.setColorIndex(0);
          u8g.setPrintPos(96, 19);
          u8g.print("YES");
          u8g.setColorIndex(1);

          if (pressedbut == 2) {
            parking_step = 1;
          }
        }

        if (pressedbut == 1) {
          if (cur_pos < 1 ) {
            cur_pos = cur_pos + 1;
          }
          else {
            cur_pos = 0;
          }
        }

        if (pressedbut == 3) {
          if (cur_pos > 0 ) {
            cur_pos = cur_pos - 1;
          }
          else {
            cur_pos = 1;
          }
        }
      }
      else if (parking_step == 1) {

        u8g.setPrintPos(7, 18);
        u8g.print("PARKING IN PROGRESS");
        //u8g.setPrintPos(10, 50);
        //u8g.setFont(u8g_font_6x10r);
        //u8g.print("IR_VAL=");
        //u8g.print(ir_value);
      }
      else if (parking_step == 2) {

        u8g.setPrintPos(15, 13);
        u8g.print("PARKING COMPLETE");
        u8g.setPrintPos(6, 26);
        u8g.print("PRESS CENTER TO EXIT");


        if (pressedbut == 2) {
          parking_step = 0;
          return;
        }
      }

    } while ( u8g.nextPage() );

  }
}

void manctrl_screen(void) {
  byte exit = 0;
  clearOLED();
  while (exit == 0) {

    u8g.firstPage();
    do {
      //buttoncheck();

      // turn OFF SIG_A (FC PAN) and SIG_B (SW PWM) ONF for PAN PWM on 4066
      digitalWrite(pwm_contr2, LOW);
      digitalWrite(pwm_contr1, HIGH);
      //digitalWrite(RXLED, LOW); // just for testing

      u8g.setFont(u8g_font_6x10);
      u8g.setPrintPos(8, 20);
      u8g.print("PAN CTRL");
      u8g.drawBox (88, 6, 33, 19);
      u8g.setColorIndex(0);
      u8g.setPrintPos(93, 19);
      u8g.print("EXIT");
      u8g.setColorIndex(1);


      if (digitalRead(bt_le) != 1) {
        //move left
        #ifdef SERVO_SPT
        myservo.writeMicroseconds(idle_servo + 100);
        #endif
        #ifdef SERVO_MG995
        myservo.writeMicroseconds(idle_servo + 40);
        #endif
        
      }

      else if (digitalRead(bt_ri) != 1) {
        //move right
        #ifdef SERVO_SPT
        myservo.writeMicroseconds(idle_servo - 100);
        #endif
        #ifdef SERVO_MG995
        myservo.writeMicroseconds(idle_servo - 40);
        #endif
      }
      else {
        myservo.writeMicroseconds(idle_servo);
      }

      if (digitalRead(bt_ct) != 1) {
        digitalWrite(pwm_contr2, HIGH);
        digitalWrite(pwm_contr1, LOW);
        //digitalWrite(RXLED, HIGH); // just for testing

        menuactive = 5;

        return;
      }



    } while ( u8g.nextPage() );
  }



}

void vtx_screen(void) {
  byte exit = 0;
  sa_update = 0;
  menuactive = 2;
  cur_pos = 0;
  clearOLED();
  while (exit == 0) {

    u8g.firstPage();
    do {
      buttoncheck();
      SAcontrol();

      u8g.setFont(u8g_font_6x10);

      if (relaypower == 1) {

        if (SA_available == 0) {
          u8g.setPrintPos(8, 20);
          u8g.print("NO VTX FOUND");
          u8g.drawBox (88, 6, 33, 19);
          u8g.setColorIndex(0);
          u8g.setPrintPos(93, 19);
          u8g.print("EXIT");
          u8g.setColorIndex(1);
        }

        else {
          u8g.setScale2x2();
          u8g.setPrintPos(4, 11);

          if (act_band == 0) {
            u8g.print("A");
          }
          else if (act_band == 1) {
            u8g.print("B");
          }
          else if (act_band == 2) {
            u8g.print("E");
          }
          else if (act_band == 3) {
            u8g.print("F");
          }
          else if (act_band == 4) {
            u8g.print("R");
          }

          u8g.setPrintPos(12, 11);
          u8g.print(act_ch);
          u8g.setFont(u8g_font_6x10);
          u8g.undoScale();

          u8g.setPrintPos(45, 19);
          u8g.print(act_freq);
          u8g.print("MHz");

          u8g.drawFrame (95, 6, 27, 19);
          u8g.setPrintPos(100, 19);
          u8g.print("SET");

          if (cur_pos == 0) {
            u8g.drawBox (7, 24, 12, 2);
          }

          else if (cur_pos == 1) {
            u8g.drawBox (23, 24, 12, 2);
          }

          else if (cur_pos == 2) {
            u8g.drawBox (95, 6, 27, 19);
            u8g.setColorIndex(0);
            u8g.setPrintPos(100, 19);
            u8g.print("SET");
            u8g.setColorIndex(1);
          }
        }
      }

      else {
        u8g.setPrintPos(10, 19);
        u8g.print("TURN VTX ON");
        u8g.drawBox (88, 6, 33, 19);
        u8g.setColorIndex(0);
        u8g.setPrintPos(93, 19);
        u8g.print("EXIT");
        u8g.setColorIndex(1);
        cur_pos = 2;
      }

      //u8g.drawFrame (0, 0, 128, 32);

      if (cur_pos == 2) {
        if (pressedbut == 2) {
          menuactive = 0;
          return;
        }
      }

      if (SA_available == 0) {
        if (pressedbut == 2) {
          menuactive = 0;
          return;
        }
      }

      if (pressedbut == 1) {
        if (cur_pos < 2 ) {
          cur_pos = cur_pos + 1;
        }
        else {
          cur_pos = 0;
        }
      }

      if (pressedbut == 3) {
        if (cur_pos > 0 ) {
          cur_pos = cur_pos - 1;
        }
        else {
          cur_pos = 2;
        }
      }


    } while ( u8g.nextPage() );

  }

}
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

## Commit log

2020-02-07 fixed pcb error
    [RelayCTRL.brd, RelayCTRL.sch]
2020-02-07 voltage callibration
2020-02-10 PCB Update
    [RelayCTRL.brd, RelayCTRL.sch]
2020-05-11 Corrected PCB bug (IR diode)
    [RelayCTRL.brd, RelayCTRL.sch]
2020-05-26 State LED
2020-07-09 Code Update
    • Two movement profiles for pan servos SERVO_SPT/SERVO_MG995
    • Cell count detection is more robust now

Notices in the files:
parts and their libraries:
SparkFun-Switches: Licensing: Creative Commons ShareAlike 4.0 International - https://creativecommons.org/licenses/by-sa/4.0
